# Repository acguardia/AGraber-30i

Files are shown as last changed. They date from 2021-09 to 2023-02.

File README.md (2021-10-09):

# AGraber 30i
 Projeto AGraber 30i

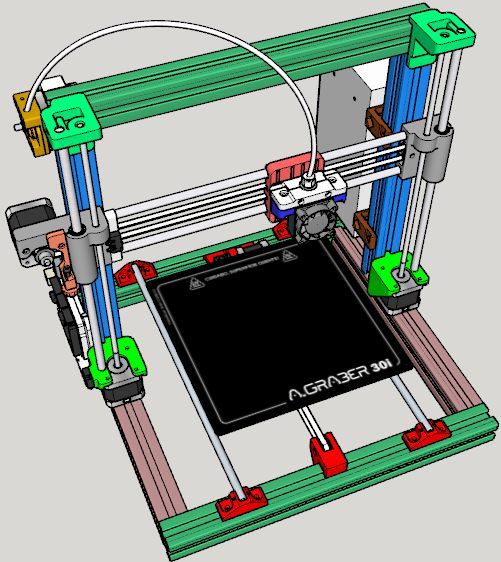
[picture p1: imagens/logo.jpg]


## Lista de peças

| Quantidade | Unidade | Descrição | Observação | Referência
| --- | --- | --- | --- | --- |
| 30 | un. | Parafusos M5x10mm | | |
| 30 | un. | Porcas Martelo para Perfil 3030 |  |  |
| 13 | un. | Porca Sextavada M3 NyLock |  |  |
| 2 | un. | Arruelas Lisas M4 |  |  |
| 3 | un. | Parafusos Allen M3x6mm |  |  |
| 3 | un. | Parafusos Allen M3x8mm |  |  |
| 18 | un. | Parafusos Allen M3x10mm |  |  |
| 5 | un. | Parafusos Allen M3x12mm |  |  |
| 17 | un. | Parafusos Allen M3x16mm |  |  |
| 20 | un. | Parafusos Allen M3x20mm |  |  |
| 14 | un. | Parafusos Allen M3x25mm |  |  |
| 2 | un. | Parafusos Allen M3x30mm |  |  |
| 1 | un. | Parafuso Allen M3 x 35mm |  |  |
| 15 | un. | Porcas Sextavadas M3 |  |  |
| 35 | un. | Arruelas Lisas M3 |  |  |
| 2 | un. | Arruelas Lisas 1/8" | Carro X, não deixar a correia escapar do carro |  |
| 2 | un. | Imãs Neodimio Redondo 4x2 |  |  |
| 4 | un. | Molas  8 voltas, 6mm diâmetro, 16mm de altura | Suspensão da Mesa Aquecida |  |
| 1 | un. | Extrusora Movtech | Opcional | [link](http://movtech.commercesuite.com.br/pecas/extrusora-direta-para-filamento-de-1-75-mm) |
| 4 | un. | Motores de Passo Nema 17 | Minimo de 3,5 Kgf.cm² e 1,0A. IDEAL  4,0 Kgf.cm² x 1,2A ou 1,7A |  |
| 1 | un. | Motor de Passo Nema 17 | Mínimo de 4,0 Kgf.cm² e 1,0A. Usado na Extrusora. |  |
| 2 | un. | Polias 20 dentes para correia GT2 de 6mm | Para motores do X e do Y |  |
| 2 | metros | Correia GT2 | Alma de fibra de vidro |  |
| 2 | un. | Polias tensoras GT2 de 20 dentes |  | [link](https://drive.google.com/file/d/1bXyFb1ZX8IkSU3b9ArEZUrr9N2AHh8Xp/view?usp=sharing) |
| 12 | un. | Rolamentos Lineares LM8UU |  |  |
| 2 | un. | Fuso Trapezoidal TR8 300mm passo 2 ou 4 |  |  |
| 2 | un. | Castanhas em Latão para Fuso TR8 passo 2 ou 4 |  |  |
| 2 | un. | Acoplador Rigido 5mmx8mm |  | [link](https://drive.google.com/file/d/1EUii7QB27qDGHcbwsaBblk0aZYnUJjxj/view?usp=sharing) |
| 2 | un. | Guia lisa, redonda, temperada, retificada, cromada 8mm x 320mm | Eixo Z |  |
| 2 | un. | Guia lisa, redonda, temperada, retificada, cromada 8mm x 340mm | Eixo Y |  |
| 2 | un. | Guia lisa, redonda, temperada, retificada, cromada 8mm x 400mm | Eixo X |  |
| 1 | un. | HotEnd E3D V5 (ou V6) com Termistor e Cartucho Aquecedor |  | [link](https://files.e3d-online.com/Drawings/E3Dv5_Assembly_Manual.pdf) |
| 1 | un. | Termistor 100K para ser usado na Mesa |  |  |
| 1 | un. | Mesa Aquecida 12V x 11A Modelo MK2b |  |  |
| 3 | un. | Chave Micro Switch KW11-3Z-3 c/ Curva 3T 250V |  | [link](https://www.eletrodex.com.br/kw11-3z-chave-micro-switch-5a.html) |
| 1 | un. | Microinterruptor de Ação Rápida 3A (BAL) |  | [link](https://www.eletrodex.com.br/chave-micro-switch-kw10b-com-haste.html) |
| 1 | un. | Servomotor SG90 9G |  | [link](https://www.eletrodex.com.br/motor-micro-servo-9g-sg90.html) |
| 1 | un. | Fonte 12V x 30A |  |  |
| 1 | un. | Placa controladora MKS E3D |  | [link](https://docs.google.com/document/d/1ZxwCf2RIq6IFCnWf0M5GBYYxGvryVqx1Z4gsOB5kWik/edit?usp=sharing) |
| 4 | un. | Drive de Motor de Passo TMC2208 ou TMC2209 ou TMC2225 |  | [link](https://docs.google.com/document/d/1ZxwCf2RIq6IFCnWf0M5GBYYxGvryVqx1Z4gsOB5kWik/edit?usp=sharing) |
| 1 | un. | LCD Mini 12864 RGB Neopixel |  |  |
| 1 | un. | Fan 40x40x10mm 12V | 5200 RPM ou 6000 RPM | [link](https://www.bottobrazil.com.br/dc-fan-40x40x10-mm) |
| 1 | un. | Fan 40x40x10mm 12V | 7000 RPM | [link](https://www.bottobrazil.com.br/dc-fan-40x40x10-mm) |
| 1 | un. | Cabo USB | Arduino <-> Computador |  |
| 1 | un. | Shield Módulo FET IRF520 |  | [link](https://drive.google.com/file/d/14vC7S0iVztOzO6d8JMr-301xOb8ngQ0q/view?usp=sharing) |
| 1 | metros | Fio Flexível 1mm² Vermelho | Fio de Conexão da Fonte ao Conector de 5A da Ramps |  |
| 1 | metros | Fio Flexível 1mm² Preto | Fio de Conexão da Fonte ao Conector de 5A da Ramps |  |
| 1 | metros | Fio Flexível 1,5mm² Vermelho | Fio de Conexão da Fonte ao Conector de 11A da Ramps | [link](https://www.eletrodex.com.br/cabinho-flexivel-1-50-mm-70-300v.html) |
| 1 | metros | Fio Flexível 1,5mm² Preto | Fio de Conexão da Fonte ao Conector de 11A da Ramps | [link](https://www.eletrodex.com.br/cabinho-flexivel-1-50-mm-70-300v.html) |
| 3 | metros | Fio Flexível 1,5mm² de Silicone para 200 °C | Fio de Conexão da Mesa à Ramps |  |
| 10 | metros | Flat AWG 26 de 6 vias | Fio para Conexões dos Fans, Microchaves fim de curso, Módulos, etc. | [link](https://www.eletrodex.com.br/cabo-flat-colorido-awg26.html) |
| 1 | un. | Cabo de Força 2P Paralelo 2x0,75mm² com 1,5m |  | [link](https://www.eletrodex.com.br/cabo-de-forca-rabicho-2pinos-paralelo-c-1-5m.html) |
| 100 | un. | Cinta Hellermann 2,5mmx100mm |  |  |
| 1 | KIT | PEÇAS IMPRESSAS PARA O PROJETO |  | [link](https://www.thingiverse.com/thing:3436936) |
| 1 | un. | Carro Y AGraber em alumínio ou ACM de 1/8" de espessura. |  | [link](https://www.thingiverse.com/thing:3436937) |

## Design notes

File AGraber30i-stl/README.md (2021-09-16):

# agraber30i-stl
Repositório com os STLs para montagem da AGraber 30i

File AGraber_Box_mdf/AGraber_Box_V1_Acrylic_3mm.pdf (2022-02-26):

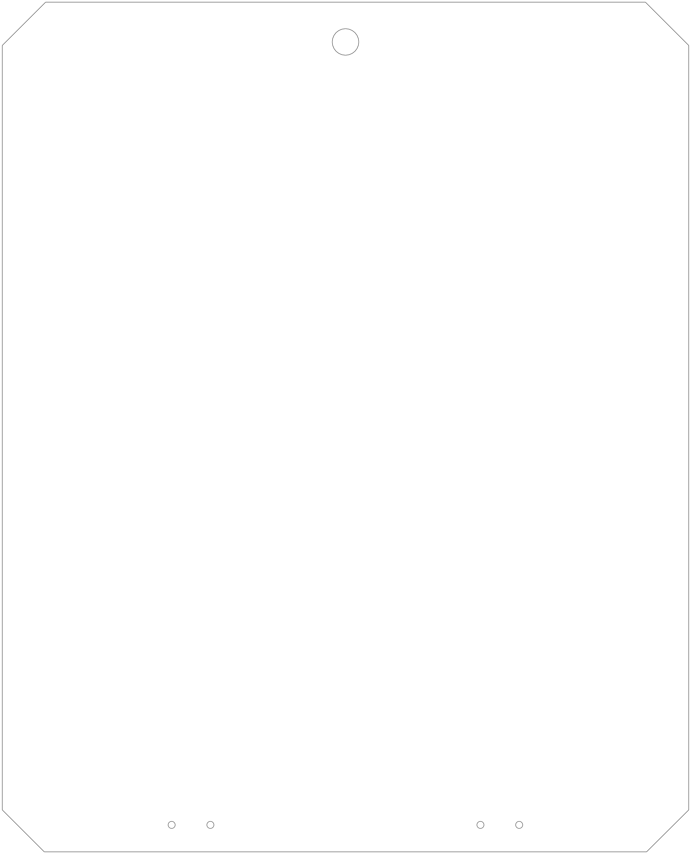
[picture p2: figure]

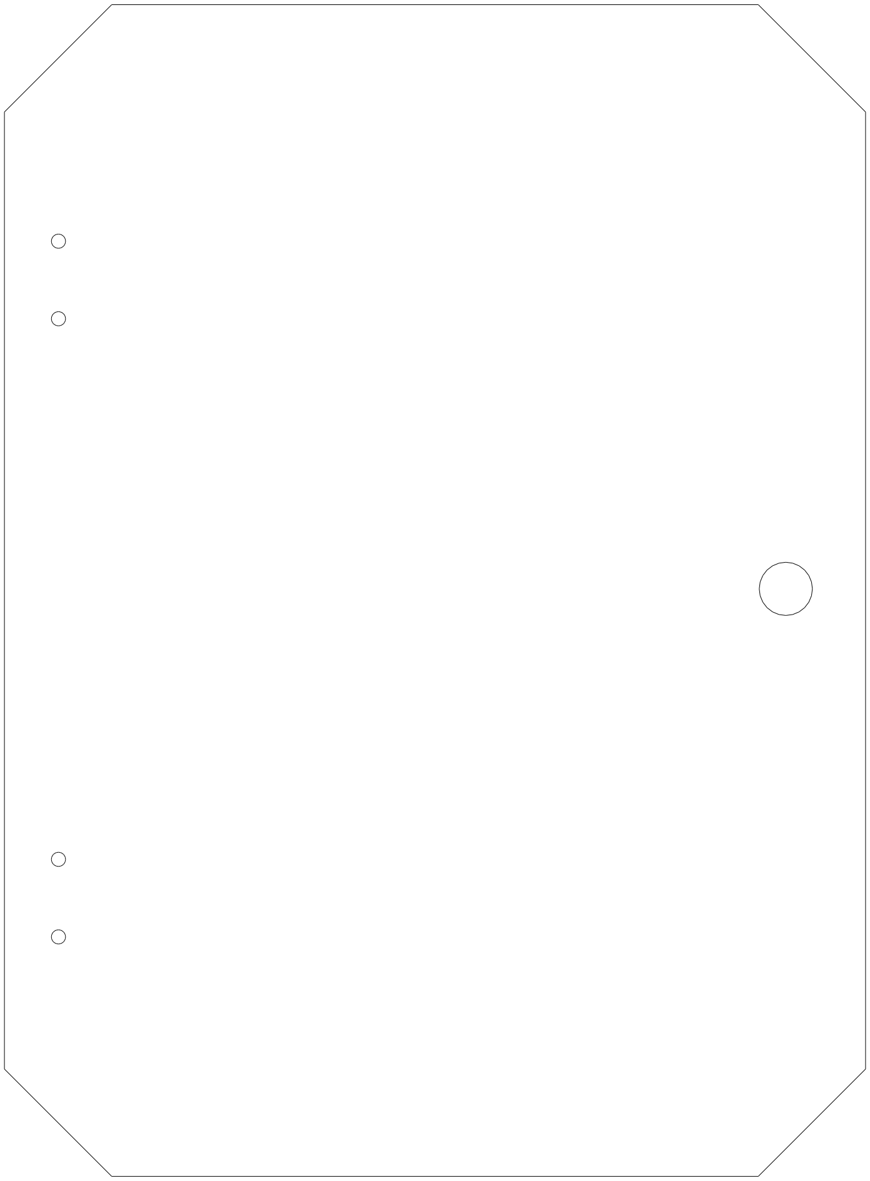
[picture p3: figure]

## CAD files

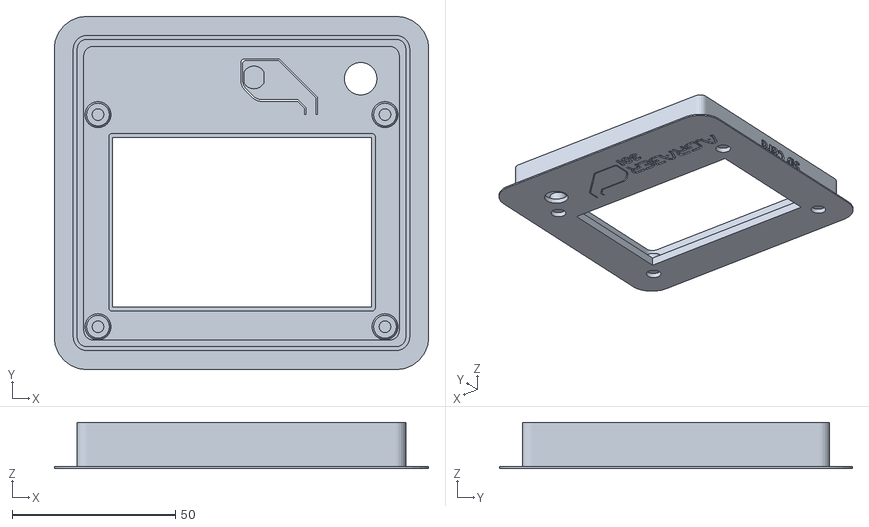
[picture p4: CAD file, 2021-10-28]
AGraber30i-stl/LCD/LCD_FULL_AGRABER_BRIM_B.stl
114.8 x 108.2 x 14.1

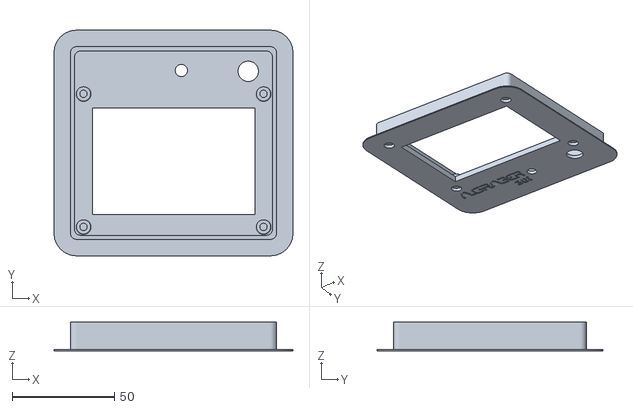
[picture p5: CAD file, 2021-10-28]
AGraber30i-stl/LCD/LCD_FULL_AGRABER_BRIM_A.stl
116.8 x 110.2 x 14.1

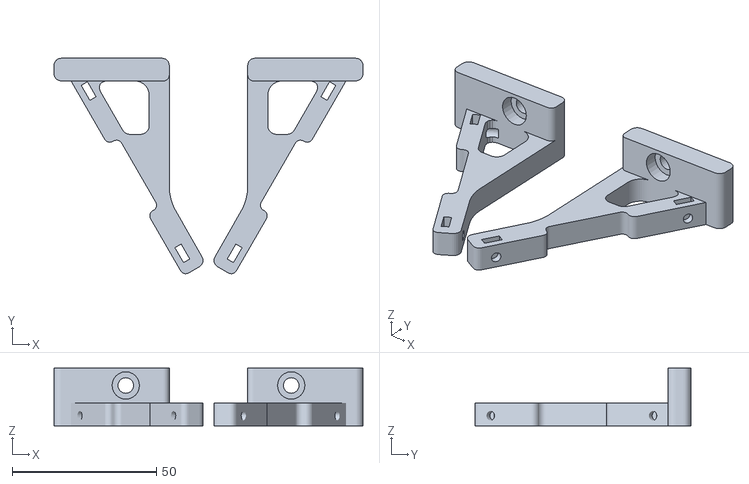
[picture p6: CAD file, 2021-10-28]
AGraber30i-stl/LCD/SUPPORT_LCD_FULL_AGRABER.stl
107.2 x 74.8 x 20.0

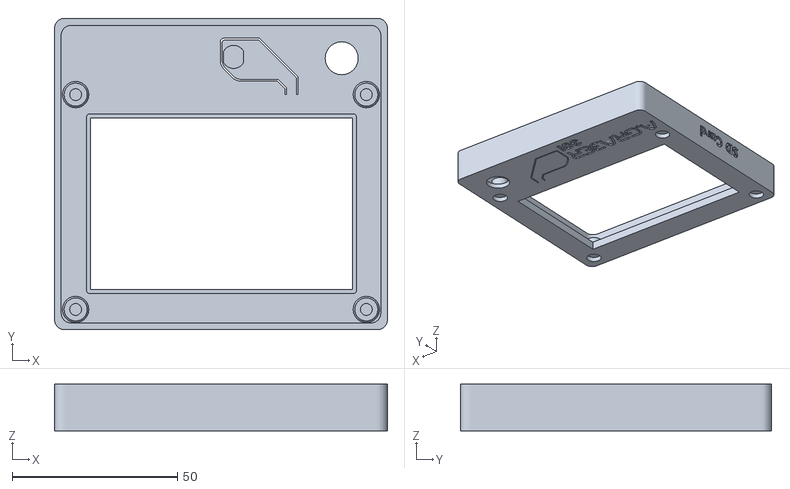
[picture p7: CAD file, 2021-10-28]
AGraber30i-stl/LCD/LCD_FULL_AGRABER_Cover.stl
100.8 x 94.2 x 14.1

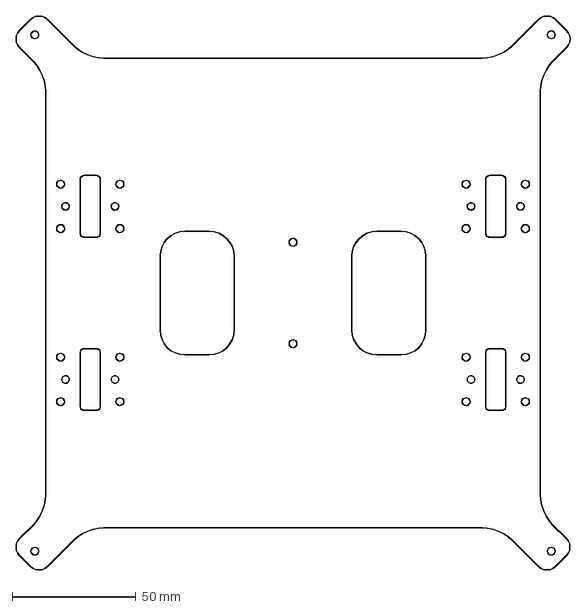
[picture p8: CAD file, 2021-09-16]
AGraber30i-dxf/MESA AGraber_30I.dxf
224.2 x 224.2 mm

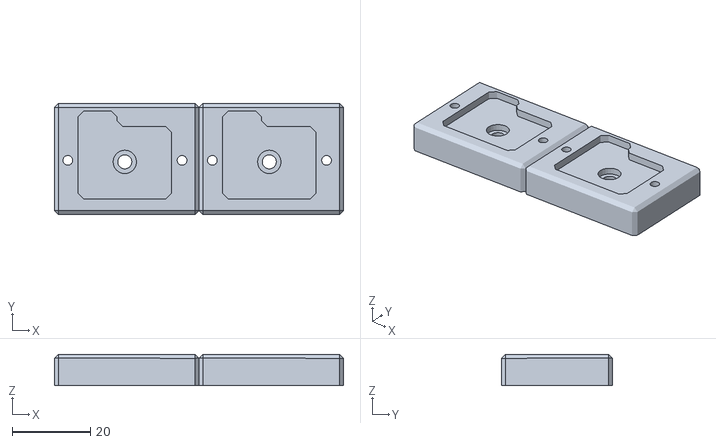
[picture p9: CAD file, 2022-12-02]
AGraber30i-stl/Acessorios/Berco_FET.stl
74.0 x 28.5 x 8.04

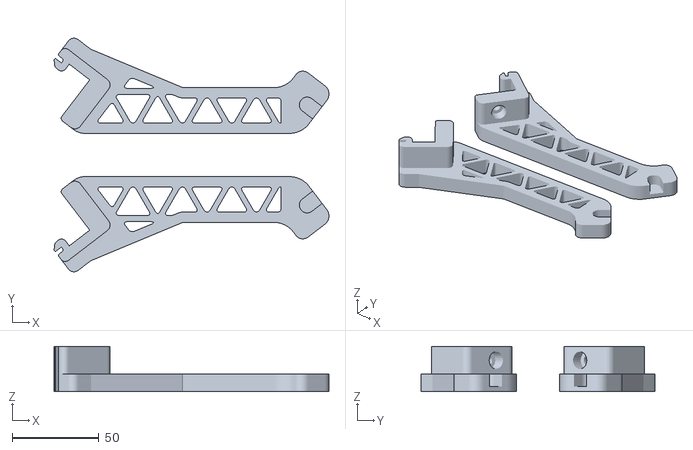
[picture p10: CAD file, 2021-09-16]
AGraber30i-stl/Acessorios/Suporte de Filamento/Suporte_Filamento_V2.stl
158.8 x 134.9 x 26.0

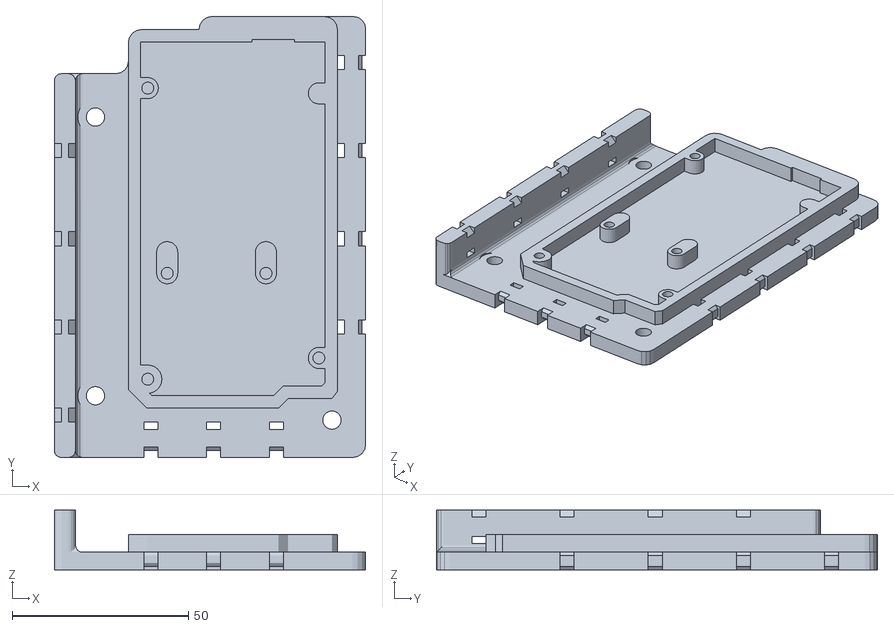
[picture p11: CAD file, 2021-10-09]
AGraber30i-stl/Acessorios/Suporte Ramps/Suporte_Ramps_M5.stl
88.3 x 125.0 x 17.0

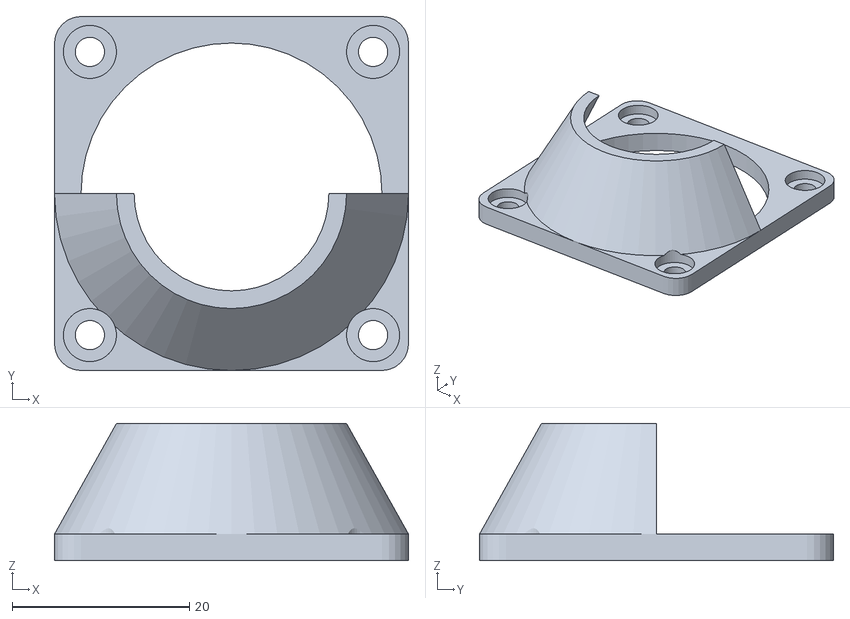
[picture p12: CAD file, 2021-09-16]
AGraber30i-stl/Eixo X/Carro_X/Air_Block_AGraber_40x40_V2.stl
40.0 x 40.0 x 15.5

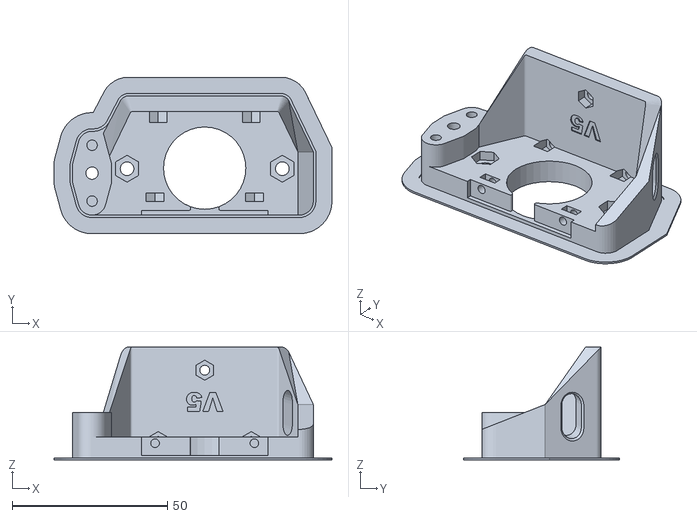
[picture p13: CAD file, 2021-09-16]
AGraber30i-stl/Eixo X/Carro_X/HotEnd_V5/3DTouch/Suporte_V5_Bowden_3DTouch_Brim.stl
89.5 x 50.4 x 36.4

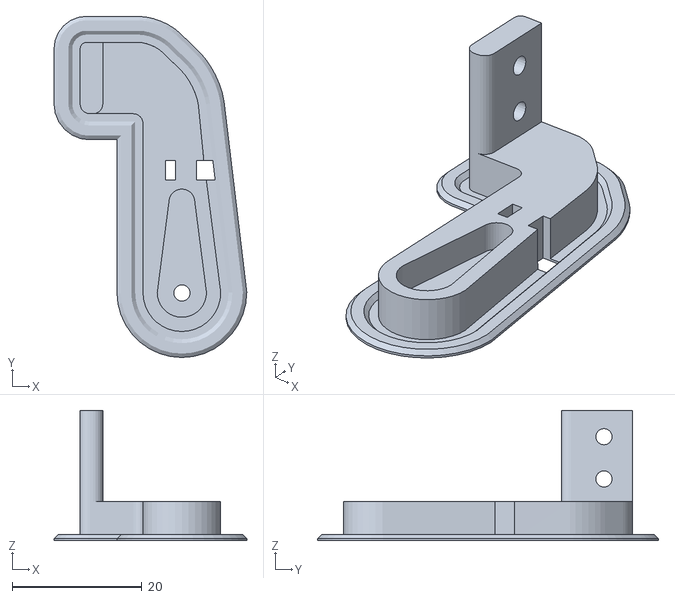
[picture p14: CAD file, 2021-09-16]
AGraber30i-stl/Eixo X/Carro_X/HotEnd_V5/BAL_V5/V5_Braco_Servo_Bal_Brim.stl
29.7 x 52.6 x 20.1

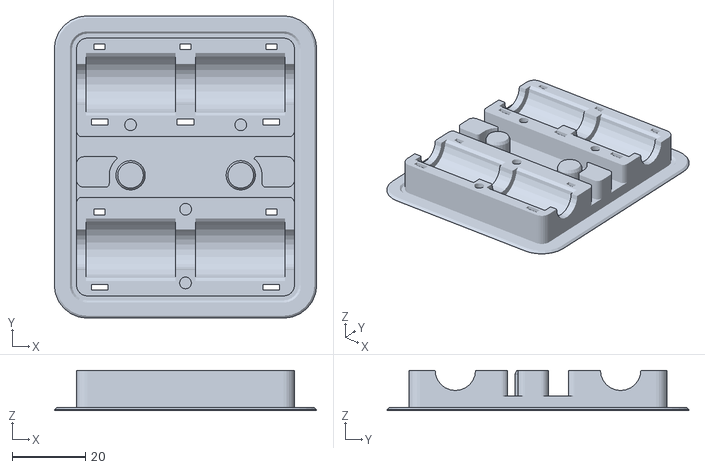
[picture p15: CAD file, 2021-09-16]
AGraber30i-stl/Eixo X/Carro_X/HotEnd_V5/Carro_X_V5_Tras.stl
71.4 x 82.2 x 11.0

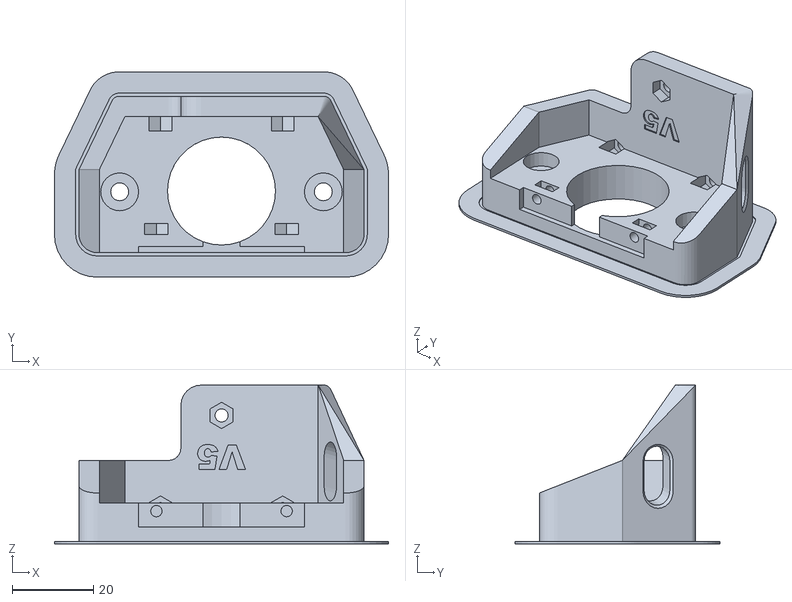
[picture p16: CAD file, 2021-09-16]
AGraber30i-stl/Eixo X/Carro_X/HotEnd_V5/Movtech/Suporte_V5_Placa_Fixadora_3mm_Brim.stl
82.0 x 50.4 x 39.0

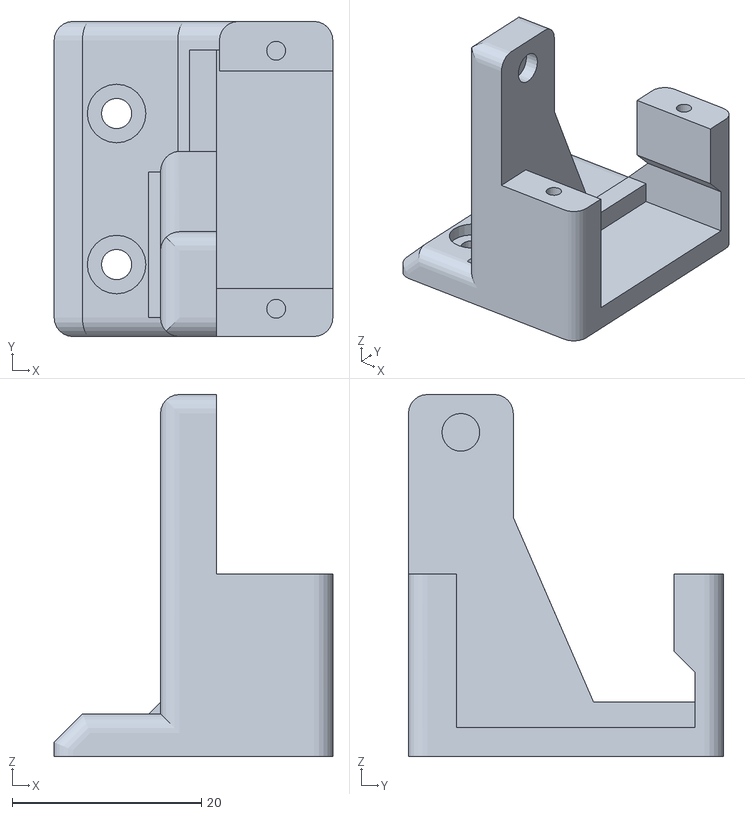
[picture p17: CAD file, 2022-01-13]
AGraber30i-stl/Eixo X/Carro_X/HotEnd_V6/BAL_V6/V6_Suporte_Servo_BAL.stl
29.5 x 33.3 x 38.3

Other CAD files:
AGraber30i-stl/Acessorios/Capa da Fonte _ Edson Brusque/PSU_BN-360_Lower_Cover_V2.stl
AGraber30i-stl/Acessorios/Capa da Fonte/Capa_Suporte_Fonte_AGraber.stl
AGraber30i-stl/Eixo X/Carro_X/HotEnd_V6/Suporte_E3DV6_BL_Touch.stl
AGraber30i-stl/Eixo X/X_Ends/TR8/Adaptador_Porca_M5_Motor.stl
AGraber30i-montagem/3030.skp
AGraber30i-stl/Acessorios/Capa da Fonte _ Edson Brusque/PSU_BN-360_Lower_Cover.stl
AGraber30i-stl/Acessorios/Capa da Fonte _ Edson Brusque/PSU_BN-360_Upper_Belt.stl
AGraber30i-stl/Acessorios/Capa da Fonte _ Edson Brusque/PSU_BN-360_Upper_Belt_V2.stl
AGraber30i-stl/Acessorios/Capa da Fonte/Suporte_Fonte_AGraber.stl
AGraber30i-stl/Acessorios/Fixador_Fonte_V4B.stl
AGraber30i-stl/Acessorios/Gabarito_Y_80mm.stl
AGraber30i-stl/Acessorios/Gabarito_Z_76,5mm.stl
AGraber30i-stl/Acessorios/Porca_Martelo_M3_3030_V2.stl
AGraber30i-stl/Acessorios/Porca_T_M3.stl
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

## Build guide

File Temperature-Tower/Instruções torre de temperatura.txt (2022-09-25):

Inserir essa linha de comando no START G-CODE do Prusa Slicer:

TUNING_TOWER COMMAND="SET_HEATER_TEMPERATURE HEATER=extruder" PARAMETER=TARGET START=235 STEP_DELTA=-5 STEP_HEIGHT=10

Parâmetros:
START = Temperatura inicial da impressão da torre
STEP_DELTA = Variação de temperatura em cada 'bloco' da torre
STEP_HEIGHT = Altura (mm) de cada 'bloco' de temperatura da torre

Agradeciento especial aos membros do grupo de apoiadores do projeto:
Salsicha Pires
Odair Gonçalves

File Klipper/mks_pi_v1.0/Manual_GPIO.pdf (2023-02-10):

Projeto AGraber, por Antonio C. Guardia

Manual para utilizar os pinos GPIOs da placa MKS Pi V1.0

Uma das funcionalidades do GPIOs de uma placa Pi (MKS, Raspbery, Orange, etc.) é poder acionar dispositivos ou ler sensores, sem que seja necessário o uso da placa escrava, no caso de se utilizar o Klipper e também do Octoprint.

Este manual vai passar o passo a passo para que se possa fazer o acionamento ou leitura do estado dos pinos GPIOs da placa MKS Pi V1.0 e, futuramente, para a placa Orange Pi Zero 2.

A primeira coisa é que o sistema, no caso Linux, já esteja instalado juntamente com o Klipper, Moonraker e Mainsail/Fluidd.

Em seguida, vamos adicionar o processador da placa como uma segunda MCU, para isso, siga os passos abaixo – ATENÇÃO, UTILIZE UM DOS COMANDOS ABAIXO (1a. ou 1b. dependendo da versão do seu kernel Linux – a opção 1b. é para versões mais recentes). (fonte: https://www.klipper3d.org/RPi_microcontroller.html):

1a.
cd ~/klipper/
sudo cp "./scripts/klipper‐mcu‐start.sh" /etc/init.d/klipper_mcu
sudo update‐rc.d klipper_mcu defaults

1b.
cd ~/klipper/
sudo cp ./scripts/klipper‐mcu.service /etc/systemd/system/ sudo systemctl enable klipper‐mcu.service

cd ~/klipper/
make menuconfig

Nesse menu, selecione “Micro‐controller Achitecture (Linux process)”, use a barra de espaços para isso, depois digite Q para salvar e sair:

3.

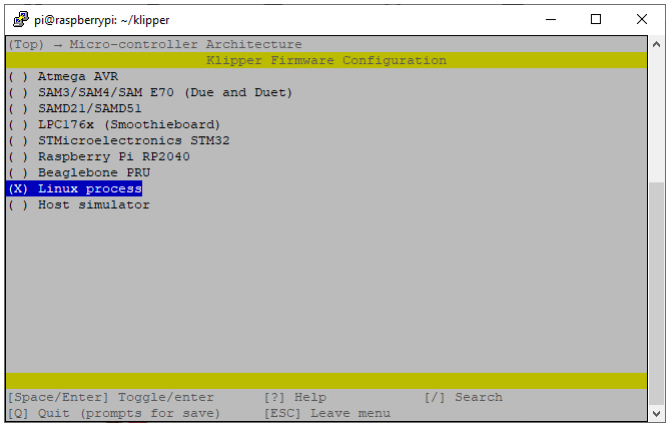
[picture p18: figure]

sudo service klipper stop
make flash
sudo service klipper start

Vamos adicionar a linha abaixo no arquivo printer.cfg:

[mcu host]
serial: /tmp/klipper_host_mcu

Em seguida, vamos criar um arquivo de configuração (regras) para dar acesso ao grupo de usuário, no caso da MKS PI é “mks” e no caso do Orange Pi Zero 2 é “orangepi”. Para isso digite no prompt:

sudo nano /etc/udev/rules.d/60‐gpiod.rules

Copie e cole essas linhas no editor de texto que abriu:

# udev rules for gpio port access through libgpiod

SUBSYSTEM=="gpio", KERNEL=="gpiochip[0‐4]", GROUP="mks", MODE="0660"

Pressione CTRL+X e, em seguida, Y para salvar e fechar o arquivo criado:

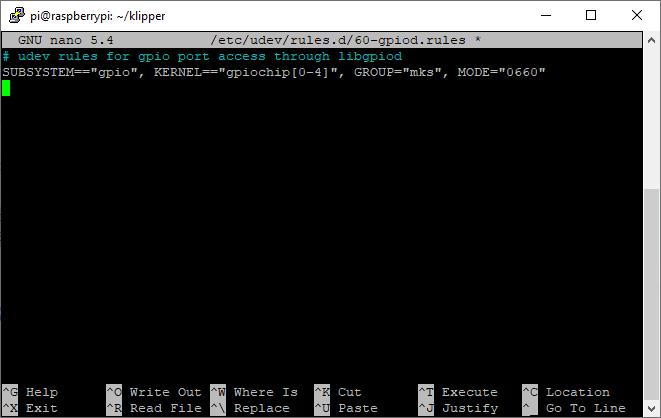
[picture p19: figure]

Reinicie o sistema com:

sudo reboot

Após o reboot, instale o utilitário GpioID pelo comando:
Esse utilitário vai te ajudar a encontrar os pinos configurados tanto no Klipper, quanto no Moonraker.

sudo apt install gpiod

Sua execução se dá pelo comando, e ele vai listar todos os “blocos” GPIOs que a placa tiver:

sudo gpioinfo

Em seguida instale o WiringOP:

git clone https://github.com/orangepi‐xunlong/wiringOP.git cd wiringOP
./build clean
./build

Sua execução se dá pelo comando:

gpio readall

No Klipper, abra o arquivo moonraker.conf e adicione essas linhas: ATENÇÃO, NO ITEM “[file_manager]” adicione apenas a linha em verde.

[file_manager]
queue_gcode_uploads: True
config_path: /home/pi/klipper_config log_path: /home/pi/klipper_logs

[job_queue]
load_on_startup: True

[power AGraber]
type: gpio
pin: gpiochip1/gpio23
off_when_shutdown: True
initial_state: off
on_when_job_queued: True
restart_klipper_when_powered: True
restart_delay: 5

A linha “pin: gpiochip1/gpio23” chama o pino 23, abaixo estão a relação dos pinos da placa MKS PI V1.0:
Talvez seja necessário adicionar um “!” antes do “gpiochip1” para inverter o estado inicial do relé, ficando, portanto, dessa forma: “pin: !gpiochip1/gpio23”

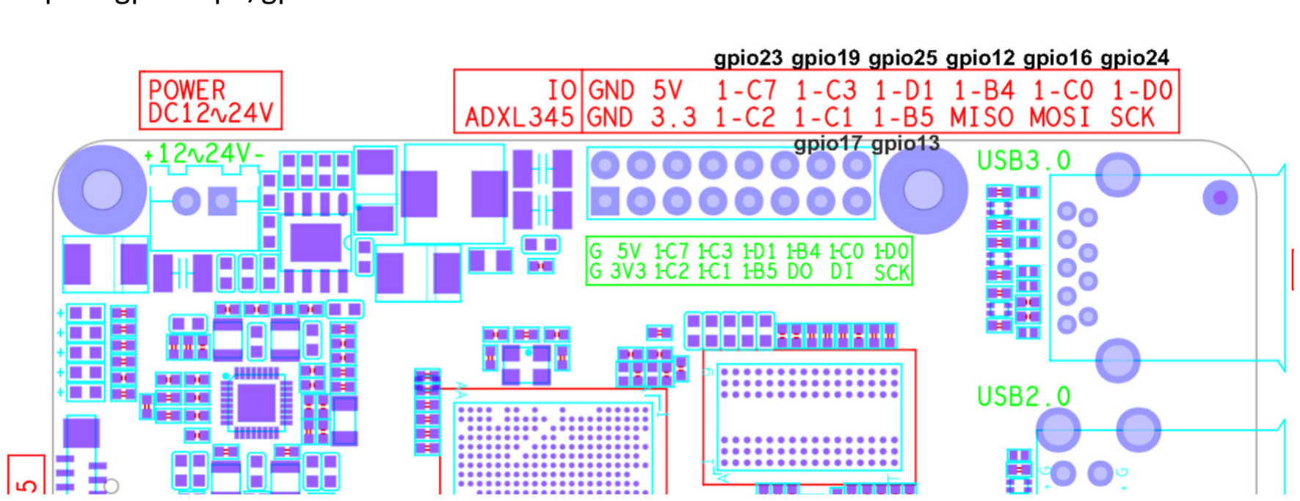
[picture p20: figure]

Para o Orange Pi Zero 2, o princípio é o mesmo, basta utilizar o esquema de GPIO da placa, que pode ser o 229, por exemplo, então ficaria “pin: gpiochip0/gpio229”:

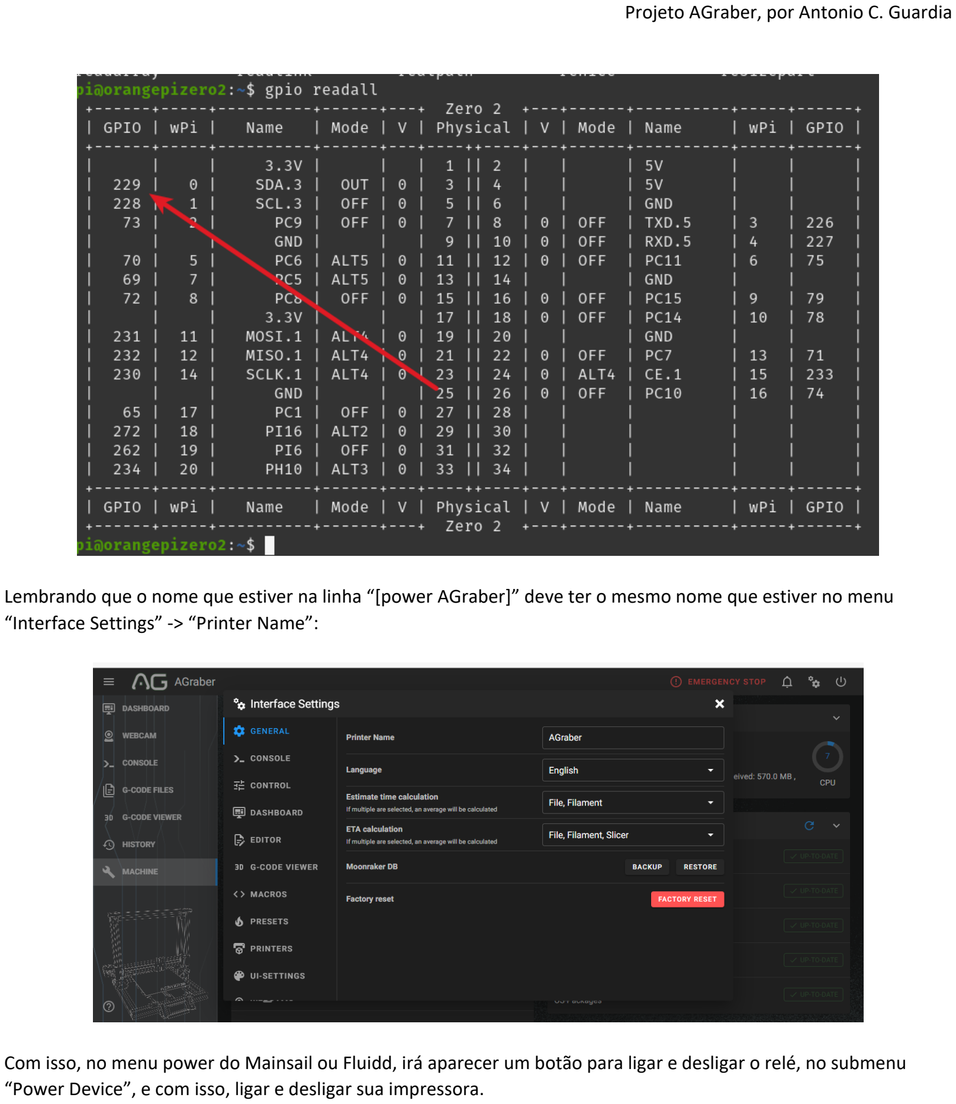
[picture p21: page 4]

Lembrando que o nome que estiver na linha “[power AGraber]” deve ter o mesmo nome que estiver no menu “Interface Settings” ‐> “Printer Name”:

Com isso, no menu power do Mainsail ou Fluidd, irá aparecer um botão para ligar e desligar o relé, no submenu “Power Device”, e com isso, ligar e desligar sua impressora.

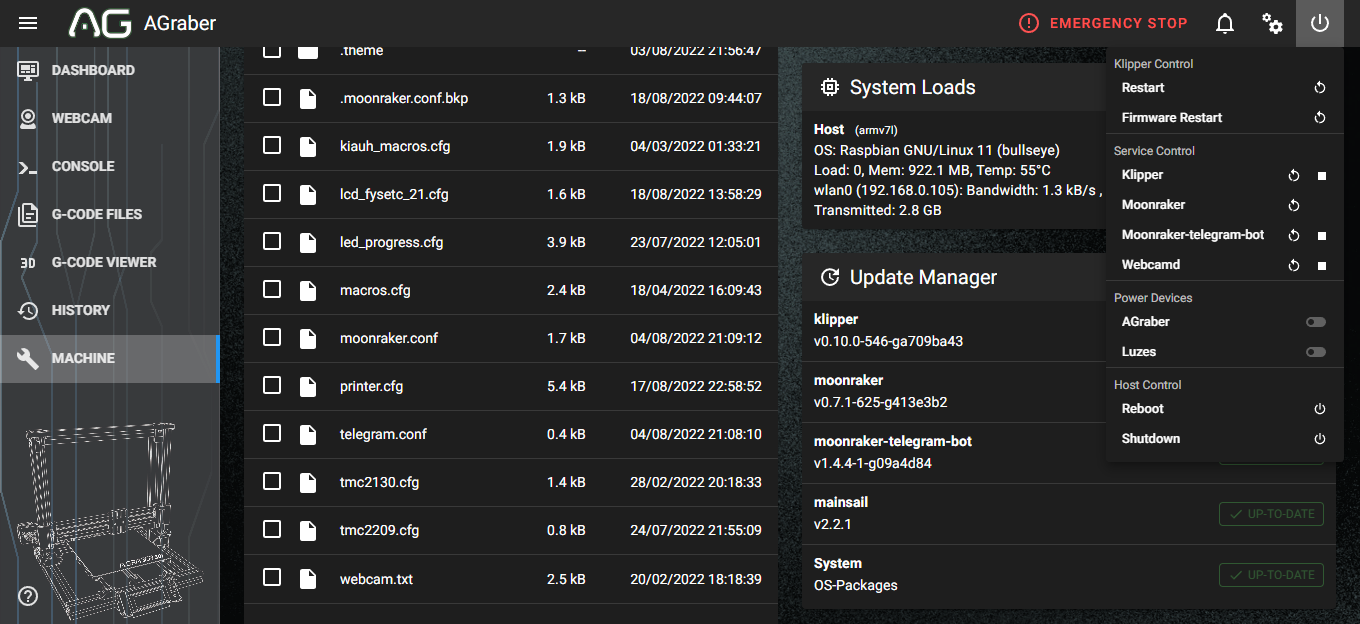
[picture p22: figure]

Um agradecimento, muito querido, ao amigo Will que ajudou no descobrimento de como fazer o acionamento pelo GPIO.

Agora vamos programar o Klipper pra desligar a impressora um tempo depois de terminar a impressão.
Eu utilizo um arquivo chamado “macros.cfg” onde salvo todas as macros que uso na impressora. Caso você não faça uso de um arquivo separado, pode salvar junto com as outras macros no printer.cfg. Lembre‐se do nome da impressora que foi falado lá em cima? Pois bem, aqui também precisa ser o mesmo nome que estiver na linha “[power AGraber]”:

[gcode_macro POWER_ON_PRINTER]
gcode:
{action_call_remote_method("set_device_power",
device="AGraber",
state="on")}
############################################################## [gcode_macro POWER_OFF_PRINTER]

gcode:
{action_call_remote_method("set_device_power",
device="AGraber",
state="off")}
############################################################## [idle_timeout]

gcode:
M84
TURN_OFF_HEATERS
M117 Turning Off in 6 minutes
UPDATE_DELAYED_GCODE ID=DELAYED_PRINTER_OFF DURATION=360 ############################################################## [delayed_gcode DELAYED_PRINTER_OFF]
initial_duration: 0.
gcode:
{% if printer.idle_timeout.state == "Idle" %}
POWER_OFF_PRINTER
{% endif %}

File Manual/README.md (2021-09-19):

# AGraber 30i
Aguarde, estamos trabalhando no manual do projeto.

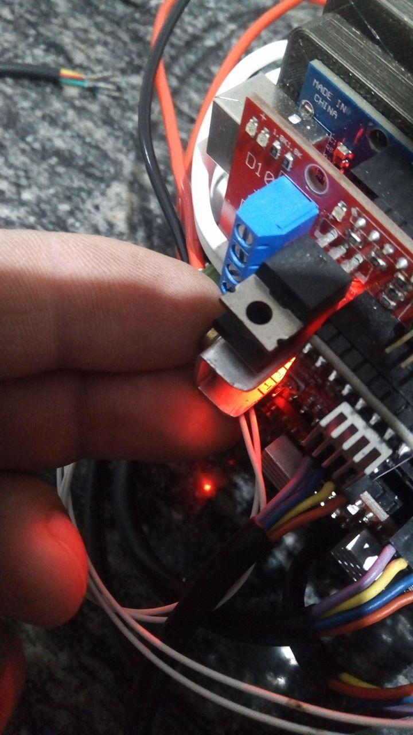
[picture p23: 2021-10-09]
AGraber30i-montagem/photo_2020-10-19_22-00-50.jpg

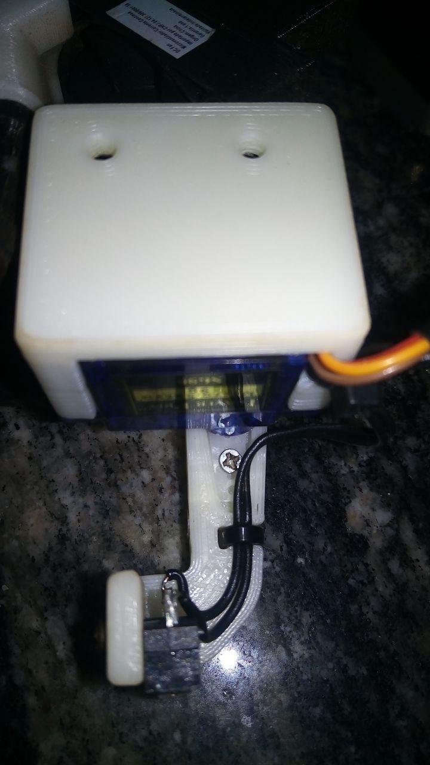
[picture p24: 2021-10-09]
AGraber30i-montagem/photo_2020-10-19_22-02-22.jpg

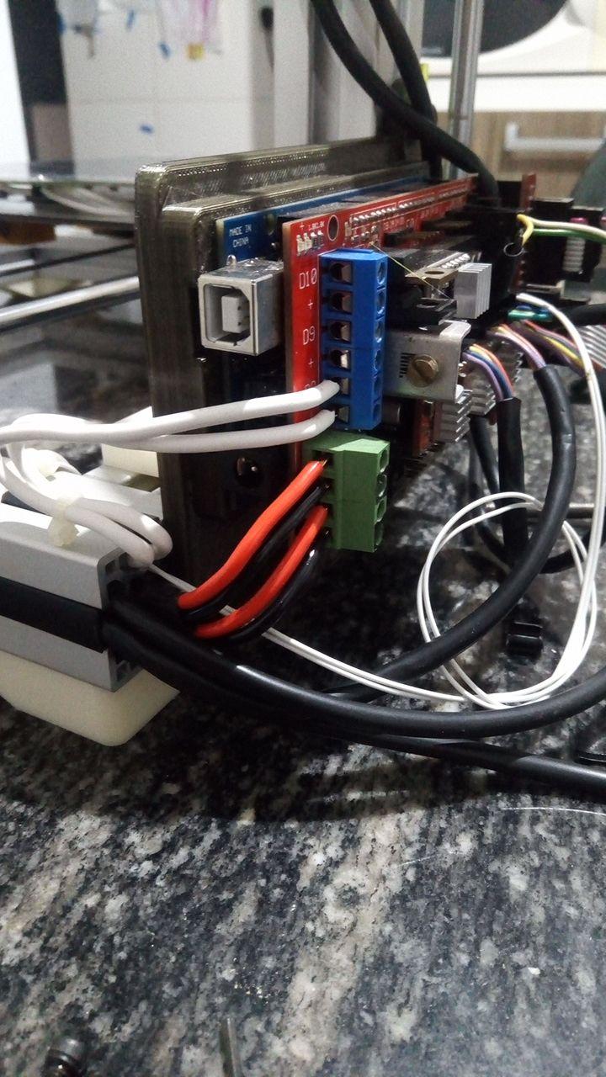
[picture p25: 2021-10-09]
AGraber30i-montagem/photo_2020-10-19_22-00-36.jpg

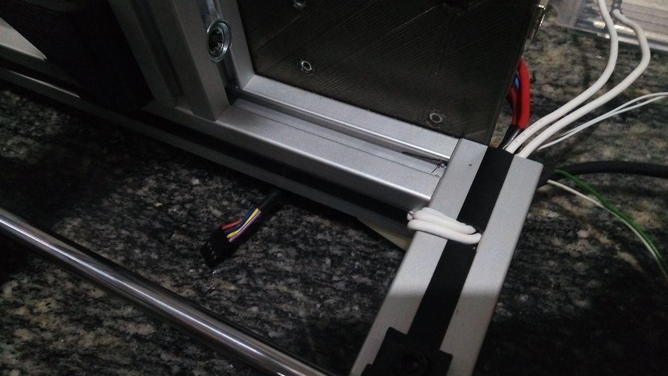
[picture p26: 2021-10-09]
AGraber30i-montagem/photo_2020-10-19_22-03-24.jpg

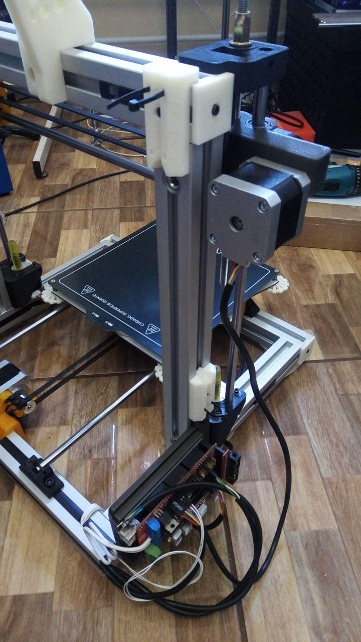
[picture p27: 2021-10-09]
AGraber30i-montagem/photo_2020-10-19_22-02-36.jpg

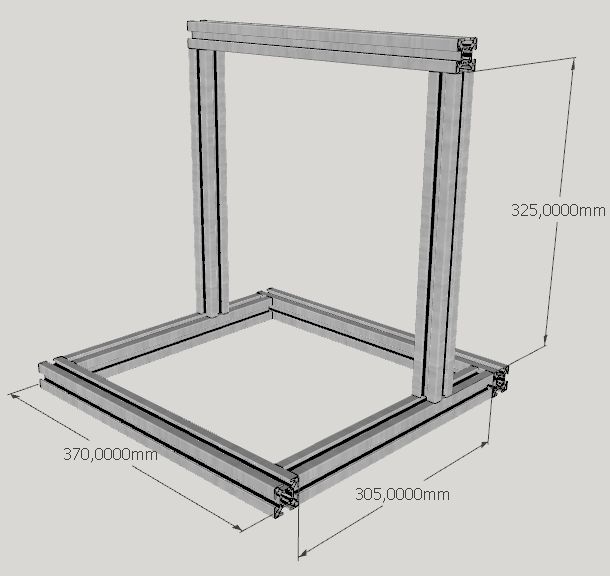
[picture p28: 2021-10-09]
AGraber30i-montagem/AGraber_30i.jpg

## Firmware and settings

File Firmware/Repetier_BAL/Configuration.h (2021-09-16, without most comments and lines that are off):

#define CONFIGURATION_H
#define NUM_EXTRUDER 1
#define MOTHERBOARD 33
#include "pins.h"
#undef FAN2_PIN
    #define FAN2_PIN -1
#undef FAN_BOARD_PIN
#define FAN_BOARD_PIN -1
#define BOARD_FAN_SPEED 255
#define BOARD_FAN_MIN_SPEED 0
#define FAN_THERMO_PIN -1
#define FAN_THERMO_MIN_PWM 128
#define FAN_THERMO_MAX_PWM 255
#define FAN_THERMO_MIN_TEMP 45
#define FAN_THERMO_MAX_TEMP 60
#define FAN_THERMO_THERMISTOR_PIN -1
#define FAN_THERMO_THERMISTOR_TYPE 1
#define BLUETOOTH_SERIAL  -1
#define BLUETOOTH_BAUD  115200
#define MIXING_EXTRUDER 0
#define DRIVE_SYSTEM 0
#define XAXIS_STEPS_PER_MM 80
#define YAXIS_STEPS_PER_MM 80
#define ZAXIS_STEPS_PER_MM 2000
#define EXTRUDER_FAN_COOL_TEMP 50
#define PDM_FOR_EXTRUDER 0
#define PDM_FOR_COOLER 0
#define DECOUPLING_TEST_MAX_HOLD_VARIANCE 20
#define DECOUPLING_TEST_MIN_TEMP_RISE 1
#define KILL_IF_SENSOR_DEFECT 0
#define RETRACT_ON_PAUSE 1
#define PAUSE_START_COMMANDS ""
#define PAUSE_END_COMMANDS ""
#define SHARED_EXTRUDER_HEATER 0
#define EXT0_X_OFFSET 0
#define EXT0_Y_OFFSET 0
#define EXT0_Z_OFFSET 0
#define EXT0_STEPS_PER_MM 147
#define EXT0_TEMPSENSOR_TYPE 14
#define EXT0_TEMPSENSOR_PIN TEMP_0_PIN
#define EXT0_HEATER_PIN HEATER_0_PIN
#define EXT0_STEP_PIN ORIG_E0_STEP_PIN
#define EXT0_DIR_PIN ORIG_E0_DIR_PIN
#define EXT0_INVERSE 0
#define EXT0_ENABLE_PIN ORIG_E0_ENABLE_PIN
#define EXT0_ENABLE_ON 0
#define EXT0_MIRROR_STEPPER 0
#define EXT0_STEP2_PIN ORIG_E0_STEP_PIN
#define EXT0_DIR2_PIN ORIG_E0_DIR_PIN
#define EXT0_INVERSE2 0
#define EXT0_ENABLE2_PIN ORIG_E0_ENABLE_PIN
#define EXT0_MAX_FEEDRATE 50
#define EXT0_MAX_START_FEEDRATE 25
#define EXT0_MAX_ACCELERATION 5000
#define EXT0_HEAT_MANAGER 1
#define EXT0_PREHEAT_TEMP 190
#define EXT0_WATCHPERIOD 1
#define EXT0_PID_INTEGRAL_DRIVE_MAX 230
#define EXT0_PID_INTEGRAL_DRIVE_MIN 40
#define EXT0_PID_PGAIN_OR_DEAD_TIME 12.7900
#define EXT0_PID_I 1.5100
#define EXT0_PID_D 40.5800
#define EXT0_PID_MAX 255
#define EXT0_ADVANCE_K 0
#define EXT0_ADVANCE_L 0
#define EXT0_ADVANCE_BACKLASH_STEPS 0
#define EXT0_WAIT_RETRACT_TEMP 180
#define EXT0_WAIT_RETRACT_UNITS 0
#define EXT0_SELECT_COMMANDS ""
#define EXT0_DESELECT_COMMANDS ""
#define EXT0_EXTRUDER_COOLER_PIN 5
#define EXT0_EXTRUDER_COOLER_SPEED 255
#define EXT0_DECOUPLE_TEST_PERIOD 12000
#define EXT0_JAM_PIN 4                            //ALTERADO, ERA -1 DESABILITADO
#define EXT0_JAM_PULLUP 0
#define FEATURE_RETRACTION 1
#define AUTORETRACT_ENABLED 1
#define RETRACTION_LENGTH 2
#define RETRACTION_LONG_LENGTH 10
#define RETRACTION_SPEED 30
#define RETRACTION_Z_LIFT 0
#define RETRACTION_UNDO_EXTRA_LENGTH 10
#define RETRACTION_UNDO_EXTRA_LONG_LENGTH 50
#define RETRACTION_UNDO_SPEED 4                   //VELOCIDADE DE EXTRUSAO, ERA 20
#define FILAMENTCHANGE_X_POS 0
#define FILAMENTCHANGE_Y_POS 0
#define FILAMENTCHANGE_Z_ADD  2
#define FILAMENTCHANGE_REHOME 1
#define FILAMENTCHANGE_SHORTRETRACT 5
#define FILAMENTCHANGE_LONGRETRACT 50
#define JAM_METHOD 2                             //(2) CHAVE ABERTA QUANDO FALTA FILAMENTO; (3) CHAVE FECHADA QUANTO FALTA FILAMENTO
#define JAM_STEPS 220
#define JAM_SLOWDOWN_STEPS 320
#define JAM_SLOWDOWN_TO 70
#define JAM_ERROR_STEPS 500
#define JAM_MIN_STEPS 10
#define JAM_ACTION 1
#define RETRACT_DURING_HEATUP true
#define PID_CONTROL_RANGE 20
#define SKIP_M109_IF_WITHIN 2
#define SCALE_PID_TO_MAX 1
#define TEMP_HYSTERESIS 0
#define EXTRUDE_MAXLENGTH 100
#define NUM_TEMPS_USERTHERMISTOR0 0
#define USER_THERMISTORTABLE0 {}
#define NUM_TEMPS_USERTHERMISTOR1 0
#define USER_THERMISTORTABLE1 {}
#define NUM_TEMPS_USERTHERMISTOR2 0
#define USER_THERMISTORTABLE2 {}
#define GENERIC_THERM_VREF 5
#define GENERIC_THERM_NUM_ENTRIES 33
#define HEATER_PWM_SPEED 1
#define COOLER_PWM_SPEED 0
#define HAVE_HEATED_BED 1
#define HEATED_BED_PREHEAT_TEMP 55
#define HEATED_BED_MAX_TEMP 120
#define SKIP_M190_IF_WITHIN 3
#define HEATED_BED_SENSOR_TYPE 14
#define HEATED_BED_SENSOR_PIN TEMP_1_PIN
#define HEATED_BED_HEATER_PIN HEATER_1_PIN
#define HEATED_BED_SET_INTERVAL 5000
#define HEATED_BED_HEAT_MANAGER 1
#define HEATED_BED_PID_INTEGRAL_DRIVE_MAX 255
#define HEATED_BED_PID_INTEGRAL_DRIVE_MIN 80
#define HEATED_BED_PID_PGAIN_OR_DEAD_TIME   196
#define HEATED_BED_PID_IGAIN   33
#define HEATED_BED_PID_DGAIN 290
#define HEATED_BED_PID_MAX 255
#define HEATED_BED_DECOUPLE_TEST_PERIOD 300000
#define MIN_EXTRUDER_TEMP 160
#define MAXTEMP 275
#define MIN_DEFECT_TEMPERATURE -10
#define MAX_DEFECT_TEMPERATURE 290
#define MILLISECONDS_PREHEAT_TIME 30000
#define SUPPORT_LASER 0
#define LASER_PIN -1
#define LASER_ON_HIGH 1
#define LASER_WARMUP_TIME 0
#define LASER_PWM_MAX 255
#define LASER_WATT 2
#define SUPPORT_CNC 0
#define CNC_WAIT_ON_ENABLE 300
#define CNC_WAIT_ON_DISABLE 0
#define CNC_ENABLE_PIN -1
#define CNC_ENABLE_WITH 1
#define CNC_DIRECTION_PIN -1
#define CNC_DIRECTION_CW 1
#define CNC_PWM_MAX 255
#define CNC_RPM_MAX 8000
#define CNC_SAFE_Z 150
#define DEFAULT_PRINTER_MODE 0
#define MULTI_ZENDSTOP_HOMING 0
#define ENDSTOP_PULLUP_X_MIN true
#define ENDSTOP_X_MIN_INVERTING true
#define MIN_HARDWARE_ENDSTOP_X true
#define ENDSTOP_PULLUP_Y_MIN true
#define ENDSTOP_Y_MIN_INVERTING true
#define MIN_HARDWARE_ENDSTOP_Y true
#define ENDSTOP_PULLUP_Z_MIN true
#define ENDSTOP_Z_MIN_INVERTING false               //Chave opto -> False
#define MIN_HARDWARE_ENDSTOP_Z true
#define ENDSTOP_PULLUP_Z2_MINMAX true
#define ENDSTOP_Z2_MINMAX_INVERTING false
#define MINMAX_HARDWARE_ENDSTOP_Z2 false
#define ENDSTOP_PULLUP_X_MAX true
#define ENDSTOP_X_MAX_INVERTING false
#define MAX_HARDWARE_ENDSTOP_X false
#define ENDSTOP_PULLUP_Y_MAX true
#define ENDSTOP_Y_MAX_INVERTING false
#define MAX_HARDWARE_ENDSTOP_Y false
#define ENDSTOP_PULLUP_Z_MAX true
#define ENDSTOP_Z_MAX_INVERTING false
#define MAX_HARDWARE_ENDSTOP_Z false
#define ENDSTOP_PULLUP_X2_MIN true
#define ENDSTOP_PULLUP_Y2_MIN true
#define ENDSTOP_PULLUP_Z2_MINMAX true
#define ENDSTOP_PULLUP_X2_MAX true
#define ENDSTOP_PULLUP_Y2_MAX true
#define ENDSTOP_X2_MIN_INVERTING false
#define ENDSTOP_Y2_MIN_INVERTING false
#define ENDSTOP_X2_MAX_INVERTING false
#define ENDSTOP_Y2_MAX_INVERTING false
#define MIN_HARDWARE_ENDSTOP_X2 false
#define MIN_HARDWARE_ENDSTOP_Y2 false
#define MAX_HARDWARE_ENDSTOP_X2 false
#define MAX_HARDWARE_ENDSTOP_Y2 false
#define MINMAX_HARDWARE_ENDSTOP_Z2 false
#define X2_MIN_PIN -1
#define X2_MAX_PIN -1
#define Y2_MIN_PIN -1
#define Y2_MAX_PIN -1
#define Z2_MINMAX_PIN -1
#define max_software_endstop_r true
#define min_software_endstop_x false
#define min_software_endstop_y false
#define min_software_endstop_z false
#define max_software_endstop_x true
#define max_software_endstop_y true
#define max_software_endstop_z true
#define DOOR_PIN -1
#define DOOR_PULLUP 1
#define DOOR_INVERTING 1
#define ENDSTOP_X_BACK_MOVE 5
#define ENDSTOP_Y_BACK_MOVE 5
#define ENDSTOP_Z_BACK_MOVE 2
#define ENDSTOP_X_RETEST_REDUCTION_FACTOR 3
#define ENDSTOP_Y_RETEST_REDUCTION_FACTOR 3
#define ENDSTOP_Z_RETEST_REDUCTION_FACTOR 3
#define ENDSTOP_X_BACK_ON_HOME 1
#define ENDSTOP_Y_BACK_ON_HOME 1
#define ENDSTOP_Z_BACK_ON_HOME 0
#define ALWAYS_CHECK_ENDSTOPS 0
#define MOVE_X_WHEN_HOMED 0
#define MOVE_Y_WHEN_HOMED 0
#define MOVE_Z_WHEN_HOMED 0
#define X_ENABLE_ON 0
#define Y_ENABLE_ON 0
#define Z_ENABLE_ON 0
#define DISABLE_X 0
#define DISABLE_Y 0
#define DISABLE_Z 0
#define DISABLE_E 0
#define INVERT_X_DIR 1
#define INVERT_X2_DIR 0
#define INVERT_Y_DIR 0
#define INVERT_Y2_DIR 0
#define INVERT_Z_DIR 0
#define INVERT_Z2_DIR 0
#define INVERT_Z3_DIR 0
#define INVERT_Z4_DIR 0
#define X_HOME_DIR -1
#define Y_HOME_DIR -1
#define Z_HOME_DIR -1
#define X_MAX_LENGTH 200
#define Y_MAX_LENGTH 200
#define Z_MAX_LENGTH 180
#define X_MIN_POS 0
#define Y_MIN_POS 0
#define Z_MIN_POS 0
#define DISTORTION_CORRECTION 0
#define DISTORTION_CORRECTION_POINTS 5
#define DISTORTION_LIMIT_TO 2
#define DISTORTION_CORRECTION_R 100
#define DISTORTION_PERMANENT 0
#define DISTORTION_UPDATE_FREQUENCY 15
#define DISTORTION_START_DEGRADE 0.5
#define DISTORTION_END_HEIGHT 1
#define DISTORTION_EXTRAPOLATE_CORNERS 0
#define DISTORTION_XMIN 10
#define DISTORTION_YMIN 10
#define DISTORTION_XMAX 190
#define DISTORTION_YMAX 190
#define FEATURE_BABYSTEPPING 1
#define BABYSTEP_MULTIPLICATOR 10
#define DELTA_SEGMENTS_PER_SECOND_PRINT 180 // Move accurate setting for print moves
#define DELTA_SEGMENTS_PER_SECOND_MOVE 70 // Less accurate setting for other moves
#define EXACT_DELTA_MOVES 1
#define DELTA_HOME_ON_POWER 0
#define DELTASEGMENTS_PER_PRINTLINE 24
#define STEPPER_INACTIVE_TIME 30L
#define MAX_INACTIVE_TIME 0L
#define MAX_FEEDRATE_X 200
#define MAX_FEEDRATE_Y 200
#define MAX_FEEDRATE_Z 2
#define HOMING_FEEDRATE_X 60
#define HOMING_FEEDRATE_Y 60
#define HOMING_FEEDRATE_Z 2
#define HOMING_ORDER HOME_ORDER_YXZ
#define ZHOME_PRE_RAISE 1         //(0) DESABILITA SUBIR O Z NO HOMING; (1) SOBE O Z SO QUANDO O Z_MIN ESTIVER ACIONADO; (2) SOBE O Z SEMPRE QUE FIZER O HOME_Z
#define ZHOME_PRE_RAISE_DISTANCE 3
#define RAISE_Z_ON_TOOLCHANGE 0
#define ZHOME_MIN_TEMPERATURE 0
#define ZHOME_HEAT_ALL 1
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

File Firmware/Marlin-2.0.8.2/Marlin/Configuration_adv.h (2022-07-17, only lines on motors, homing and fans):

#define E0_AUTO_FAN_PIN -1	//PA2
#define E1_AUTO_FAN_PIN -1
#define E2_AUTO_FAN_PIN -1
#define E3_AUTO_FAN_PIN -1
#define E4_AUTO_FAN_PIN -1
#define E5_AUTO_FAN_PIN -1
#define E6_AUTO_FAN_PIN -1
#define E7_AUTO_FAN_PIN -1
#define CHAMBER_AUTO_FAN_PIN -1
#define COOLER_AUTO_FAN_PIN -1
#define COOLER_FAN_PIN -1
#define HOMING_BUMP_MM      { 5, 5, 2 }       // (mm) Backoff from endstops after first bump
#define HOMING_BUMP_DIVISOR { 2, 2, 20 }       // Re-Bump Speed Divisor (Divides the Homing Feedrate)
#define QUICK_HOME                          // If G28 contains XY do a diagonal move first
#define MICROSTEP_MODES { 16, 16, 16, 16, 16, 16 } // [1,2,4,8,16]
  #define BABYSTEP_WITHOUT_HOMING
#define ADVANCED_PAUSE_FEATURE
  #define ADVANCED_PAUSE_PURGE_FEEDRATE        5  // (mm/s) Extrude feedrate (after loading). Should be slower than load feedrate.
  #define ADVANCED_PAUSE_PURGE_LENGTH        120  // (mm) Length to extrude after loading.
  #define ADVANCED_PAUSE_RESUME_PRIME          0  // (mm) Extra distance to prime nozzle after returning from park.
    #define X_CURRENT       580        // (mA) RMS current. Multiply by 1.414 for peak current.
    #define X_CURRENT_HOME  X_CURRENT  // (mA) RMS current for sensorless homing
    #define X_MICROSTEPS     16        // 0..256
    #define Y_CURRENT       580
    #define Y_CURRENT_HOME  Y_CURRENT
    #define Y_MICROSTEPS     16
    #define Z_CURRENT       800
    #define Z_CURRENT_HOME  Z_CURRENT
    #define Z_MICROSTEPS      16
    #define E0_CURRENT      750
    #define E0_MICROSTEPS    16
    #define CURRENT_STEP_DOWN     50  // [mA]
    #define REPORT_CURRENT_CHANGE
  #define HYBRID_THRESHOLD
  #define X_HYBRID_THRESHOLD      80  // [mm/s]
  #define X2_HYBRID_THRESHOLD     80
  #define Y_HYBRID_THRESHOLD      80
  #define Y2_HYBRID_THRESHOLD     80
  #define Z_HYBRID_THRESHOLD       4
  #define Z2_HYBRID_THRESHOLD      2
  #define Z3_HYBRID_THRESHOLD      2
  #define Z4_HYBRID_THRESHOLD      2
  #define E0_HYBRID_THRESHOLD     50
  #define E1_HYBRID_THRESHOLD     30
  #define E2_HYBRID_THRESHOLD     30
  #define E3_HYBRID_THRESHOLD     30
  #define E4_HYBRID_THRESHOLD     30
  #define E5_HYBRID_THRESHOLD     30
  #define E6_HYBRID_THRESHOLD     30
  #define E7_HYBRID_THRESHOLD     30

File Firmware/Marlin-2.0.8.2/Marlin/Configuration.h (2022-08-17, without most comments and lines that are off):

#pragma once
#define CONFIGURATION_H_VERSION 02000801
#define STRING_CONFIG_H_AUTHOR "(AC Guardia, 2021)" // Who made the changes.
#define SHOW_BOOTSCREEN
#define SHOW_CUSTOM_BOOTSCREEN
#define SERIAL_PORT 1
#define BAUDRATE 250000
#define SERIAL_PORT_2 2
  #define MOTHERBOARD BOARD_MKS_ROBIN_E3D_V1_1 //MKS ROBIN E3D V1.1
#define CUSTOM_MACHINE_NAME "AGraber 30i"
#define EXTRUDERS 1
#define DEFAULT_NOMINAL_FILAMENT_DIA 1.75
#define PSU_CONTROL
#define PSU_NAME "Power Supply"
  #define PSU_ACTIVE_STATE  LOW     // Set 'LOW' for ATX, 'HIGH' for X-Box
#define TEMP_SENSOR_0 24
#define TEMP_SENSOR_1 0
#define TEMP_SENSOR_2 0
#define TEMP_SENSOR_3 0
#define TEMP_SENSOR_4 0
#define TEMP_SENSOR_5 0
#define TEMP_SENSOR_6 0
#define TEMP_SENSOR_7 0
#define TEMP_SENSOR_BED 25
#define TEMP_SENSOR_PROBE 0
#define TEMP_SENSOR_CHAMBER 0
#define TEMP_SENSOR_COOLER 0
#define DUMMY_THERMISTOR_998_VALUE  60
#define DUMMY_THERMISTOR_999_VALUE 220
#define MAX_REDUNDANT_TEMP_SENSOR_DIFF 10
#define TEMP_RESIDENCY_TIME         10  // (seconds) Time to wait for hotend to "settle" in M109
#define TEMP_WINDOW                  1  // (°C) Temperature proximity for the "temperature reached" timer
#define TEMP_HYSTERESIS              3  // (°C) Temperature proximity considered "close enough" to the target
#define TEMP_BED_RESIDENCY_TIME     10  // (seconds) Time to wait for bed to "settle" in M190
#define TEMP_BED_WINDOW              1  // (°C) Temperature proximity for the "temperature reached" timer
#define TEMP_BED_HYSTERESIS          3  // (°C) Temperature proximity considered "close enough" to the target
#define TEMP_CHAMBER_RESIDENCY_TIME 10  // (seconds) Time to wait for chamber to "settle" in M191
#define TEMP_CHAMBER_WINDOW          1  // (°C) Temperature proximity for the "temperature reached" timer
#define TEMP_CHAMBER_HYSTERESIS      3  // (°C) Temperature proximity considered "close enough" to the target
#define HEATER_0_MINTEMP   5
#define HEATER_1_MINTEMP   5
#define HEATER_2_MINTEMP   5
#define HEATER_3_MINTEMP   5
#define HEATER_4_MINTEMP   5
#define HEATER_5_MINTEMP   5
#define HEATER_6_MINTEMP   5
#define HEATER_7_MINTEMP   5
#define BED_MINTEMP        5
#define CHAMBER_MINTEMP    5
#define HEATER_0_MAXTEMP 275
#define HEATER_1_MAXTEMP 275
#define HEATER_2_MAXTEMP 275
#define HEATER_3_MAXTEMP 275
#define HEATER_4_MAXTEMP 275
#define HEATER_5_MAXTEMP 275
#define HEATER_6_MAXTEMP 275
#define HEATER_7_MAXTEMP 275
#define BED_MAXTEMP      150
#define CHAMBER_MAXTEMP  60
#define HOTEND_OVERSHOOT 15   // (°C) Forbid temperatures over MAXTEMP - OVERSHOOT
#define BED_OVERSHOOT    10   // (°C) Forbid temperatures over MAXTEMP - OVERSHOOT
#define COOLER_OVERSHOOT  2   // (°C) Forbid temperatures closer than OVERSHOOT
#define PIDTEMP
#define BANG_MAX 255     // Limits current to nozzle while in bang-bang mode; 255=full current
#define PID_MAX BANG_MAX // Limits current to nozzle while PID is active (see PID_FUNCTIONAL_RANGE below); 255=full current
#define PID_K1 0.95      // Smoothing factor within any PID loop
  #define DEFAULT_Kp 36.67  //19.43
  #define DEFAULT_Ki  3.57  //1.65
  #define DEFAULT_Kd 94.08  //57.3
#define PIDTEMPBED
#define MAX_BED_POWER 255 // limits duty cycle to bed; 255=full current
  #define DEFAULT_bedKp 116.81 //64.29
  #define DEFAULT_bedKi  20.24 //6.08
  #define DEFAULT_bedKd 449.44 //452.94
#define MAX_CHAMBER_POWER 255 // limits duty cycle to chamber heater; 255=full current
  #define PID_FUNCTIONAL_RANGE 10 // If the temperature difference between the target temperature and the actual temperature
#define PREVENT_COLD_EXTRUSION
#define EXTRUDE_MINTEMP 170
#define PREVENT_LENGTHY_EXTRUDE
#define EXTRUDE_MAXLENGTH 200
#define THERMAL_PROTECTION_HOTENDS // Enable thermal protection for all extruders
#define THERMAL_PROTECTION_BED     // Enable thermal protection for the heated bed
#define THERMAL_PROTECTION_CHAMBER // Enable thermal protection for the heated chamber
#define THERMAL_PROTECTION_COOLER  // Enable thermal protection for the laser cooling
#define USE_XMIN_PLUG
#define USE_YMIN_PLUG
#define USE_ZMIN_PLUG
#define ENDSTOPPULLUPS
#define X_MIN_ENDSTOP_INVERTING false // Set to true to invert the logic of the endstop.
#define Y_MIN_ENDSTOP_INVERTING false // Set to true to invert the logic of the endstop.
#define Z_MIN_ENDSTOP_INVERTING true // Set to true to invert the logic of the endstop.
#define X_MAX_ENDSTOP_INVERTING false // Set to true to invert the logic of the endstop.
#define Y_MAX_ENDSTOP_INVERTING false // Set to true to invert the logic of the endstop.
#define Z_MAX_ENDSTOP_INVERTING false // Set to true to invert the logic of the endstop.
#define Z_MIN_PROBE_ENDSTOP_INVERTING false // Set to true to invert the logic of the probe.
#define X_DRIVER_TYPE  TMC2209
#define Y_DRIVER_TYPE  TMC2209
#define Z_DRIVER_TYPE  TMC2209
#define E0_DRIVER_TYPE TMC2209
#define DEFAULT_AXIS_STEPS_PER_UNIT   { 80, 80, 400, 83 }
#define DEFAULT_MAX_FEEDRATE          { 400, 400, 5, 25 }
#define DEFAULT_MAX_ACCELERATION      { 600, 600, 100, 5000 }
#define DEFAULT_ACCELERATION          600    // X, Y, Z and E acceleration for printing moves
#define DEFAULT_RETRACT_ACCELERATION  600    // E acceleration for retracts
#define DEFAULT_TRAVEL_ACCELERATION   800    // X, Y, Z acceleration for travel (non printing) moves
#define CLASSIC_JERK
  #define DEFAULT_XJERK  8.0
  #define DEFAULT_YJERK  8.0
  #define DEFAULT_ZJERK  0.3
#define DEFAULT_EJERK    5.0  // May be used by Linear Advance
#define S_CURVE_ACCELERATION
#define USE_PROBE_FOR_Z_HOMING
#define Z_MIN_PROBE_PIN PB1    // Pin 32 is the RAMPS default
#define BLTOUCH
#define NOZZLE_TO_PROBE_OFFSET { 35, -5, -3.250 }
#define PROBING_MARGIN 25
#define XY_PROBE_FEEDRATE (80*60)
#define Z_PROBE_FEEDRATE_FAST (3*60)
#define Z_PROBE_FEEDRATE_SLOW (Z_PROBE_FEEDRATE_FAST / 2)
#define MULTIPLE_PROBING 2
#define Z_CLEARANCE_DEPLOY_PROBE    0 // Z Clearance for Deploy/Stow
#define Z_CLEARANCE_BETWEEN_PROBES  5 // Z Clearance between probe points
#define Z_CLEARANCE_MULTI_PROBE     4 // Z Clearance between multiple probes
#define Z_PROBE_LOW_POINT          -2 // Farthest distance below the trigger-point to go before stopping
#define Z_PROBE_OFFSET_RANGE_MIN -20
#define Z_PROBE_OFFSET_RANGE_MAX 20
#define X_ENABLE_ON 0
#define Y_ENABLE_ON 0
#define Z_ENABLE_ON 0
#define E_ENABLE_ON 0 // For all extruders
#define DISABLE_X false
#define DISABLE_Y false
#define DISABLE_Z false
#define DISABLE_E false             // Disable the extruder when not stepping
#define DISABLE_INACTIVE_EXTRUDER   // Keep only the active extruder enabled
#define INVERT_X_DIR false
#define INVERT_Y_DIR true
#define INVERT_Z_DIR true
#define INVERT_E0_DIR false
#define INVERT_E1_DIR false
#define INVERT_E2_DIR false
#define INVERT_E3_DIR false
#define INVERT_E4_DIR false
#define INVERT_E5_DIR false
#define INVERT_E6_DIR false
#define INVERT_E7_DIR false
#define Z_HOMING_HEIGHT  2      // (mm) Minimal Z height before homing (G28) for Z clearance above the bed, clamps, ...
#define X_HOME_DIR -1
#define Y_HOME_DIR -1
#define Z_HOME_DIR -1
#define X_BED_SIZE 210
#define Y_BED_SIZE 200
#define X_MIN_POS 0
#define Y_MIN_POS 0
#define Z_MIN_POS 0
#define X_MAX_POS X_BED_SIZE
#define Y_MAX_POS Y_BED_SIZE
#define Z_MAX_POS 225
#define MIN_SOFTWARE_ENDSTOPS
  #define MIN_SOFTWARE_ENDSTOP_X
  #define MIN_SOFTWARE_ENDSTOP_Y
  #define MIN_SOFTWARE_ENDSTOP_Z
#define MAX_SOFTWARE_ENDSTOPS
  #define MAX_SOFTWARE_ENDSTOP_X
  #define MAX_SOFTWARE_ENDSTOP_Y
  #define MAX_SOFTWARE_ENDSTOP_Z
#define AUTO_BED_LEVELING_BILINEAR
#define RESTORE_LEVELING_AFTER_G28
  #define ENABLE_LEVELING_FADE_HEIGHT
    #define DEFAULT_LEVELING_FADE_HEIGHT 10.0 // (mm) Default fade height.
  #define SEGMENT_LEVELED_MOVES
  #define LEVELED_SEGMENT_LENGTH 5.0 // (mm) Length of all segments (except the last one)
  #define GRID_MAX_POINTS_X 3
  #define GRID_MAX_POINTS_Y GRID_MAX_POINTS_X
#define LCD_BED_LEVELING
  #define MESH_EDIT_Z_STEP  0.025 // (mm) Step size while manually probing Z axis.
  #define LCD_PROBE_Z_RANGE 3     // (mm) Z Range centered on Z_MIN_POS for LCD Z adjustment
#define LEVEL_BED_CORNERS
  #define LEVEL_CORNERS_INSET_LFRB { 30, 30, 30, 30 } // (mm) Left, Front, Right, Back insets
  #define LEVEL_CORNERS_HEIGHT      0.0   // (mm) Z height of nozzle at leveling points
  #define LEVEL_CORNERS_Z_HOP       2.0   // (mm) Z height of nozzle between leveling points
  #define LEVEL_CORNERS_LEVELING_ORDER { LF, RF, RB, LB }
#define Z_PROBE_END_SCRIPT "M500"
#define Z_SAFE_HOMING
  #define Z_SAFE_HOMING_X_POINT X_CENTER  // X point for Z homing
  #define Z_SAFE_HOMING_Y_POINT Y_CENTER  // Y point for Z homing
#define HOMING_FEEDRATE_MM_M { (50*60), (50*60), (6*60) }
#define VALIDATE_HOMING_ENDSTOPS
#define EEPROM_SETTINGS     // Persistent storage with M500 and M501
#define EEPROM_CHITCHAT       // Give feedback on EEPROM commands. Disable to save PROGMEM.
  #define EEPROM_AUTO_INIT  // Init EEPROM automatically on any errors.
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

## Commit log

2021-09-16 Projeto AGraber
    [4x_AGraber_Y.stl, 4x_AGraber_Y_M3_Brim.stl, 4x_AGraber_Y_M5.stl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]
2021-09-16 Arquivos de referências do Marlin
2021-09-16 Alteração para placa MKS Robin Nano V3
    Foi alterado a linha #default_envs = mks_robin_nano_v3.
2021-09-16 Add Marlin .zip
2021-09-16 Add zip files
    [Carro_Y.stl]
2021-09-26 ADD Fysetc LCD Cover
    [LCD_12864_Mini_DIR.stl, LCD_12864_Mini_ESQ.stl, LCD_12864_Mini_Fysetc_Frente.stl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]
2021-10-01 Aprimora README com BOM e imagem de boas vindas
2021-10-03 Adaptador pra M5
    [Adaptador_Porca_M5_Indler.stl, Adaptador_Porca_M5_Motor.stl, Adaptador_Rebite_M5_Indler.stl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]
2021-10-07 Exclusão
    exclusão de arquivos duplicados
2021-10-09 Atualização de pastas
    [4x_AGraber_Y.stl, 4x_AGraber_Y_M3_Brim.stl, 4x_AGraber_Y_M5.stl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]
2021-10-28 LCD 2004
    [SUPPORT_LCD_2004.stl, SUPPORT_LCD_2004_Dir.stl, SUPPORT_LCD_2004_Esq.stl]
2021-10-28 Peças Obsoletas
    [Disco_Ajuste_EndStop.stl, Suporte_Gatilho_EndStop.stl, Suporte_Gatilho_EndStop_Maior.stl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]
2022-01-14 ,
    ,
    [CONFIGURACAO_MKS_ROBIN_NANO_V2_V3.txt, Configuration.h, Configuration_adv.h]
2022-02-26 Klipper Files
    [Configuration.h, Configuration_adv.h, Porca_Martelo_M3_3030_V2.stl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]
2022-02-26 Add Klipper.zip
2022-03-03 Configuracao LCD Fysetc Mini 12864 2.1
    [Configuration.h, Configuration_adv.h]
2022-03-03 Atualizacao de setup
    [Configuration.h, Configuration_adv.h]
2022-07-17 Novos desenhos
    [Configuration_adv.h]
2022-08-17 Atualização Klipper
    [Configuration.h, lcd_fysetc_21.cfg, led_progress.cfg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]
2022-08-27 Move arquives
    [kiauh_macros.cfg, lcd_fysetc_21.cfg, led_progress.cfg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]
2022-08-28 Update Manual para utilizar os pinos GPIOs da placa MKS Pi V1.pdf
2022-09-23 Novos arquivos
    [Knob_Nivelar_Mesa_Menor.stl]
2022-09-25 Create Instruções torre de temperatura.txt
2022-09-25 Add STL towers
    [ABS.stl, PETG.stl, PLA.stl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]
2022-09-25 Update Instruções torre de temperatura.txt
2023-02-24 Atualização Marlin_2082.zip

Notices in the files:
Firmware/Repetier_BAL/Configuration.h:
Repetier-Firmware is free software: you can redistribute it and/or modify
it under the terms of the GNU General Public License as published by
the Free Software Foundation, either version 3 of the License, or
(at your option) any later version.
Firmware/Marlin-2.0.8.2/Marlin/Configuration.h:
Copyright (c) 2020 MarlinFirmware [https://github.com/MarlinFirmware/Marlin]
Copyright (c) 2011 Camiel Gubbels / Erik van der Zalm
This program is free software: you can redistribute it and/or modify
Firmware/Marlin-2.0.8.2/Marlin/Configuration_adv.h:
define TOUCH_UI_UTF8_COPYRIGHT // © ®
